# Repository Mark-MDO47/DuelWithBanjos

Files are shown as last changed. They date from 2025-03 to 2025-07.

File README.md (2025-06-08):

# DuelWithBanjos
Just for fun - tiny scarecrow skeletons playing banjo music, placed under the control of the UniRemote!
- https://github.com/Mark-MDO47/UniRemote
- DuelWithBanjos now at version V1.0!

A quick 38-second video demonstration:
- https://youtu.be/nwAhtAX-E6E

A story-line showing how to do Over-The-Air (OTA) Web updates to the Banjo Player ESP32.
- https://github.com/Mark-MDO47/DuelWithBanjos/blob/master/code/DuelWithBanjos/OTA_story.md

| My two little banjo players - BEFORE | My two little banjo players - AFTER<br>with new electronics and sound |
| --- | --- |
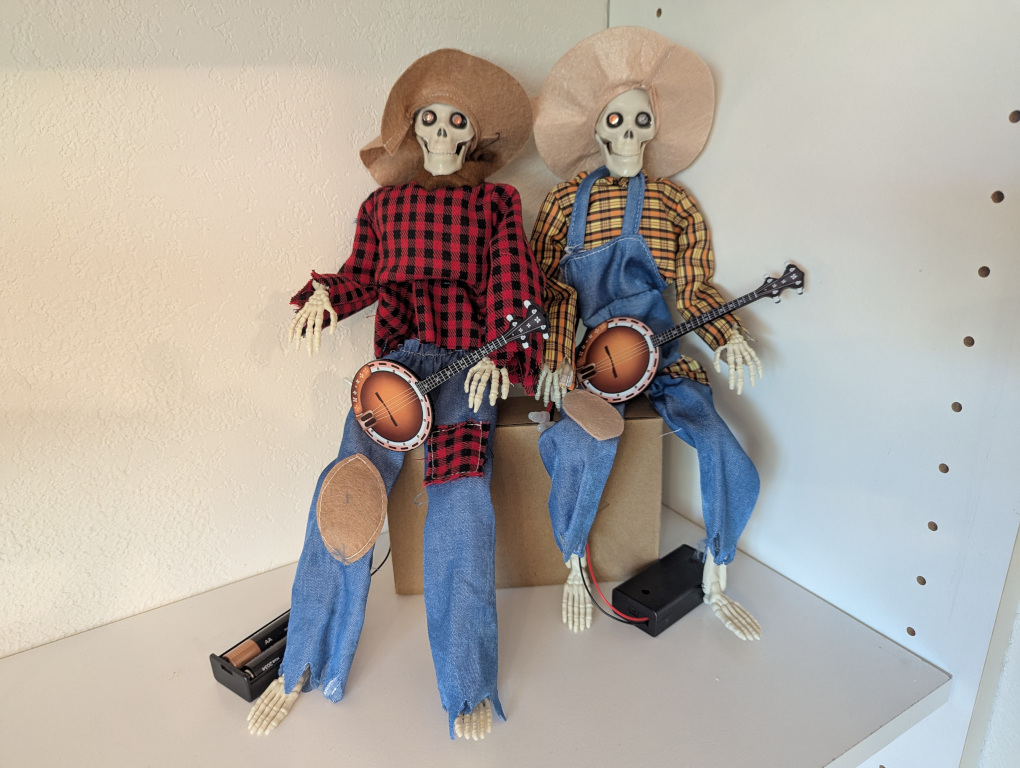
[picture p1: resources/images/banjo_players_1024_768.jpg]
My Banjo Players BEFORE
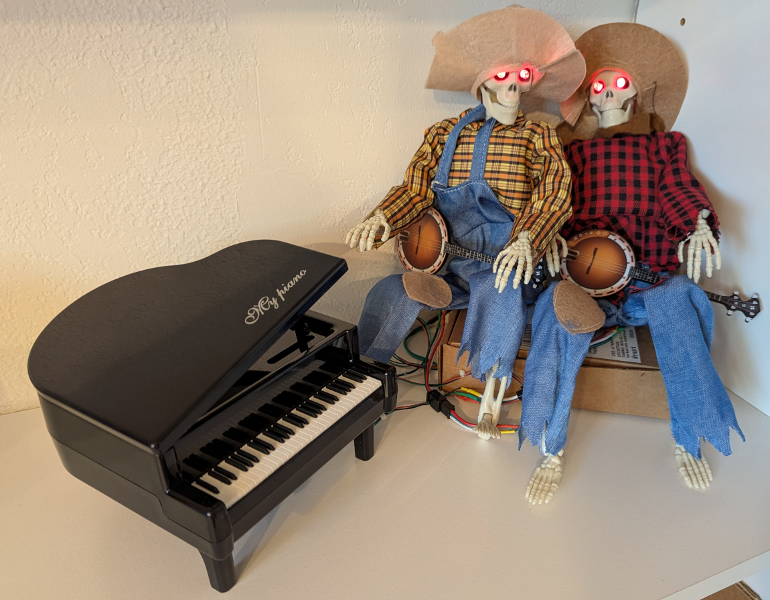
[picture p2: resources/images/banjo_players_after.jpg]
My Banjo Players AFTER upgrade
|  |  |
| **The new electronics on a prototype board** | **The new electronics inside the cardboard box** |
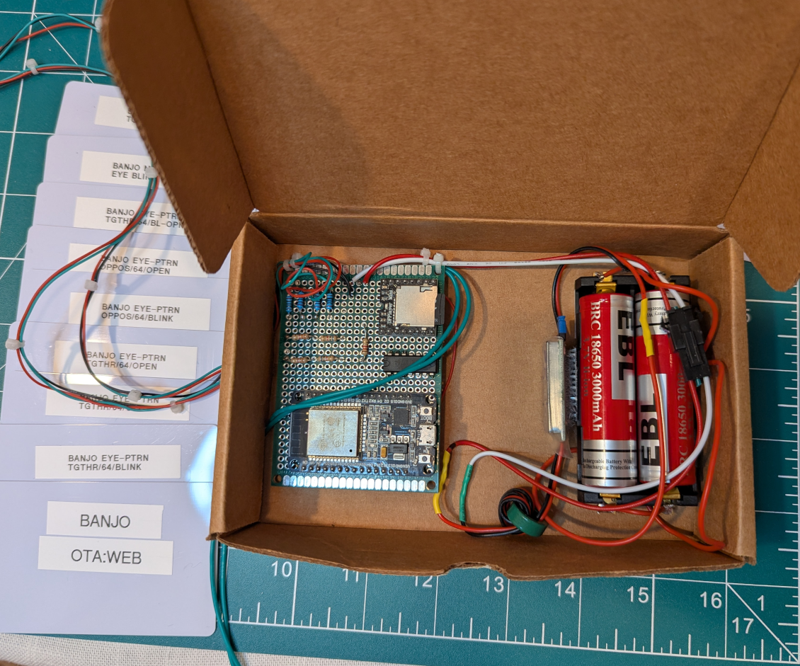
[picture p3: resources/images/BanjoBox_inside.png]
Banjo Player electronics inside cardboard box
| My ProtoBoard Banjo Player electronics |  |

**Table Of Contents**
* [Top](#duelwithbanjos "Top")
* [Introduction](#introduction "Introduction")
* [Schematic](#schematic "Schematic")
  * [Do-It-Yourself Layout Creator](#do\-it\-yourself-layout-creator "Do-It-Yourself Layout Creator")
* [Code](#code "Code")
* [Parts List](#parts-list "Parts List")
* [License](#license "License")

## Introduction
[Top](#duelwithbanjos "Top")<br>
I have two country style skeleton banjo players approximately 14 inches tall ordered from Amazon.com but apparently that exact model is no longer available there.
I think they might be similar to this one:
- https://www.amazon.com/XINANDHAO-Halloween-Animated-Skeletons-Musicians/dp/B0DC56RL1F

Version V1.0 includes the following capabilities:
- respond to controls from my UniRemote remote controller via ESP-NOW
  - https://github.com/Mark-MDO47/UniRemote
- play music using a YX5200 Audio Player which reads sound files from a MicroSD card
  - https://github.com/Mark-MDO47/AudioPlayer-YX5200
- blink LED "eyes" using Pulse Width Modulation (PWM)
  - https://github.com/Mark-MDO47/DuelWithBanjos/tree/master/code/LEDPinsPwmTemplate
- Have volume control for the sound
  - Fixed my bug; this now seems to work! I may make it more elaborate later.
- support Over-The-Air (OTA) re-programming
  - https://github.com/Mark-MDO47/DuelWithBanjos/blob/master/code/DuelWithBanjos/OTA_story.md
  - https://github.com/Mark-MDO47/UniRemote/blob/master/code/mdo_use_ota_webupdater/README.md

The future plan is to make them
- support OTA debugging via the extension "Visual Micro" for Visual Studio Code
  - I am still working on it - getting ESP-NOW, ota_webupdater, and OTA debugging to play together
  - https://www.visualmicro.com/
  - https://code.visualstudio.com/

## Schematic
[Top](#duelwithbanjos "Top")<br>
This is the schematic of the interesting part of the design, including the ESP32 module, sound control, and LED control.<br>
- The ESP32 of course has I/O at the 3.3V rail. The YX5200 uses 5V power and TTL voltage levels, which could be up to 5V.
  -  I use resistor networks to drop the YX5200 output voltages from 5V to 3.3V to be compatible with the ESP32 inputs. The ESP32 is **NOT** 5V tolerant on its inputs.
  -  The YX5200 is nominally able to work with TTL-level inputs (and 3.3V should be fine), but I use a SN74HCT125N quadruple bus buffer to raise voltages from 3.3V to 5V. I have had some issues with ESP32 outputs to WS2812B in the past and just like to beef the signal up to avoid problems.
- The 1K resistor in the path to the YX5200 RX line prevents coupling of digital noise into the sound output.
- I had to move to ESP32 pin D26 because of my horrible soldering.
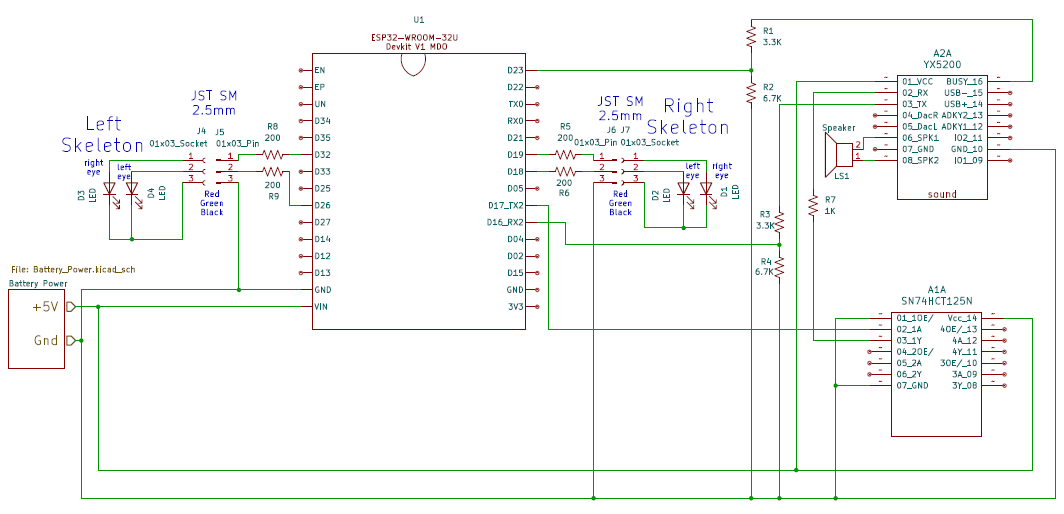
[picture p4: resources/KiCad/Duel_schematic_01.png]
Schematic of ESP32 module, sound control, and LED control


### Do-It-Yourself Layout Creator
[Top](#uniremote-\--one-remote-to-rule-them-all "Top")<br>
I didn't know about this when I did my perfboard design for Dueling with Banjos but I wish I had used DIYLC instead of hacking away at my perfboard!
- https://github.com/bancika/diy-layout-creator
- https://github.com/bancika/diy-layout-creator/releases

Here is a nice YouTube showing how to use it
- Design Circuits on Stripboard or Veroboard for FREE with DIY Layout Creator by TekSparkz - https://www.youtube.com/watch?v=mzje3eHqi2E

## Code
[Top](#duelwithbanjos "Top")<br>
The code is starting to take shape; you can find it here
- https://github.com/Mark-MDO47/DuelWithBanjos/tree/master/code/DuelWithBanjos

I wanted my PWM LED control to be automatic in between commands but also to respond to commands. I made some code to do this. Once everything is initialized, you only need to call **led_pins_pwm()** periodically from loop() to have the LED eyes follow the requested time pattern.
- https://github.com/Mark-MDO47/DuelWithBanjos/tree/master/code/LEDPinsPwmTemplate

## Parts List
[Top](#duelwithbanjos "Top")<br>
Work In Progress...

| Title | Descrip | URL | each |
| --- | --- | --- | --- |
| Skeletons | 2 @ Pose-able banjo playing skeletons | https://www.amazon.com/XINANDHAO-Halloween-Animated-Skeletons-Musicians/dp/B0DC56RL1F | $10.00 |
| ESP32 | 1 @ ESP32 Devkit V1 ESP-WROOM-32 | https://www.amazon.com/Hosyond-ESP-WROOM-32-Development-Microcontroller-Compatible/dp/B0C7C2HQ7P/ref=sr_1_4 | $3.50 |
| YX5200 | 1 @ Sound Module with MicroSD (TF) card socket | https://www.amazon.com/Organizer-YX5200-DFPlayer-Supporting-Arduino/dp/B07XXYQBNS/ref=sr_1_1 | $2.00 |
| SN74HCT125N | 1 @ Non-inverting 5.5V buffer 14-pin DIP | https://www.digikey.com/en/products/detail/texas-instruments/SN74HCT125N/376860 | $0.63 |
| Proto Board | 1 @ 3.125" x 2.25" Prototype Board | from deep in my closet | $ who-knows? |
| speaker |  Metal Shell Round Internal Magnet Speaker 2W 8 Ohm approx 1 inch | https://www.amazon.com/dp/B0177ABRQ6 | $2.80 |
| JST SM 2.5mm | 2 @ pair JST SM 2.5mm 3-pin Male/Female connectors and cables for banjo players | https://www.amazon.com/mxuteuk-Connectors-Connector-Adapter-Electrical/dp/B0DHKC3ZSF/ref=sr_1_2?th=1 | $0.45 |
| resistors | 4 @ 200-Ohm 1/4 watt through-hole resistors | https://www.digikey.com/en/products/filter/through-hole-resistors/53?s=N4IgTCBcDaIE4FMDOBLJAXA9nEBdAvkA | $0.10 |
| resistors | 1 @ 1.0-KOhm 1/4 watt through-hole resistors | https://www.digikey.com/en/products/detail/stackpole-electronics-inc/CF14JT1K00/1741314 | $0.10 |
| resistors | 2 @ 3.3-KOhm 1/4 watt through-hole resistors | https://www.digikey.com/en/products/detail/stackpole-electronics-inc/CF14JT3K30/1741376 | $0.10 |
| resistors | 2 @ 6.65-KOhm 1/4 watt through-hole resistors | https://www.digikey.com/en/products/detail/stackpole-electronics-inc/RNF14FTD6K65/1682364 | $0.10 |
| on/off latch button | 1 @ ON/Off Switch Self-Lock Micro Push Button Switch DC 30V 1A | https://www.amazon.com/gp/product/B086L2GPGX | $0.20 |
| UBEC 5V | 1 @ 5V/6V HOBBYWING 3A UBEC | https://www.aliexpress.us/item/3256805502614547.html | $1.50 |
| 18650 Battery | 2 @ 3.7V 18650 & charger<br>URL has 4 batteries plus charger so price each is inflated | https://www.amazon.com/dp/B0CP6V26QX | $5.00 |
| 18650 2-slot holder | 18650 Battery Holder 2 Slot 3.7V 18650 Battery | https://www.amazon.com/dp/B09LC13D9P | $2.60 |
| JST SM 2.5mm | 1 @ pair JST SM 2.5mm 3-pin Male/Female connectors and cables for power connection | https://www.amazon.com/mxuteuk-Connectors-Connector-Adapter-Electrical/dp/B0DHKC3ZSF/ref=sr_1_2?th=1 | $0.45 |

## License
[Top](#duelwithbanjos "Top")<br>
This repository has a LICENSE file for the Apache 2.0 License. There may be code included that I have modified from other open sources (such as Arduino, Espressif, SparkFun, Seeed Studio, DFRobot, RandomNerds, etc.). These other sources may possibly be licensed using a different license model. In such a case I will include some notation of this. Typically I will include verbatim the license in the included/modified source code, but alternatively there might be a LICENSE file in the source code area that points out exceptions to the Apache 2.0 License.

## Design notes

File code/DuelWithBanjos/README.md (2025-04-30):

# Duel With Banjos Code

My Banjo Players

**Table Of Contents**
* [Top](#duel-with-banjos-code "Top")
* [The Banjo Players](#the-banjo-players "The Banjo Players")
* [YX5200 Audio Player](#yx5200-audio-player "YX5200 Audio Player")
  * [The Music](#the-music "The Music")
  * [LICENSE for DFRobot code](#license-for-dfrobot-code "LICENSE for DFRobot code")
* [ESP32 LEDC PWM - LED Dimmer Control](#esp32-ledc-pwm-\--led-dimmer-control "ESP32 LEDC PWM - LED Dimmer Control")
* [UniRemote and ESP-NOW](#uniremote-and-esp\-now "UniRemote and ESP-NOW")
* [Over-The-Air Update](#over\-the\-air-update "Over-The-Air Update")
* [ESP32](#esp32 "ESP32")

## The Banjo Players
[Top](#duel-with-banjos-code "Top")<br>
I have two country style skeleton scarecrow banjo players approximately 14 inches tall ordered from Amazon.com but apparently that exact model is no longer available there.
I think they might be similar to this one:
- https://www.amazon.com/XINANDHAO-Halloween-Animated-Skeletons-Musicians/dp/B0DC56RL1F

The ones I have each have a 3V power supply and two very bright red LED eyes. There is no other electronics involved in them.

## YX5200 Audio Player
[Top](#duel-with-banjos-code "Top")<br>
I am providing sound for my banjo players using the YX5200 Audio Player, which is widely available from many sources. A MicroSD card is used to store the sound files.

There are some tricks to using this device in a way that many of the variants work. You may be interested to look in my repo here:
- https://github.com/Mark-MDO47/AudioPlayer-YX5200

Top view pin arrangement on YX5200 module

The music and sounds on the MicroSD card are either purchased by me or recorded/created by me. Attributions are present on the MicroSD card. The sound files are not included in this repository in respect of the copyright of the owners.

### The Music
[Top](#duel-with-banjos-code "Top")<br>
Currently the music includes
- Dueling Banjos by Curtis Mcpeake from **Curtis Mcpeake Plays Dueling Banjos & Other Bluegrass Favorites**
- Several selections from Todd Taylor's **Todd Taylor's Banjo Christmas**
- Several selections from **The Essential Patriotic Collection**
- Several selections from Garrick Ohlsson's **The Complete Chopin Piano Works Volume 10: Etudes**
- Several selections from Claudio Arrau's **Chopin: The Complete Nocturnes/The Complete Impromptus**
- A selection from Ingrid Filter's **Frederic Chopin Preludes**

### LICENSE for DFRobot code
[Top](#duel-with-banjos-code "Top")<br>
The DFRobot code (see https://www.dfrobot.com/) is not under the Apache License 2.0<br>
The license for the DFRobot code is copied into the file LICENSE_for_DFRobot_code.txt

## ESP32 LEDC PWM - LED Dimmer Control
[Top](#duel-with-banjos "Top")<br>
I am using the Espressif ESP32 Pulse Width Modulation (PWM) LED control to make the LED eyes do something interesting. This capability is similar to that available on Arduinos such as the Arduino Uno, but is specifically tailored to the ESP32. Be sure to use the new "pin-oriented" calling sequence instead of the earlier "channel-oriented" calling sequence.
- https://docs.espressif.com/projects/esp-idf/en/v5.4/esp32/api-reference/peripherals/ledc.html
- https://github.com/espressif/arduino-esp32/blob/master/docs/en/migration_guides/2.x_to_3.0.rst#ledc

You can see my method (still being refined) for having the LEDC PWM patterns play themselves here
- https://github.com/Mark-MDO47/DuelWithBanjos/blob/master/code/LEDPinsPwmTemplate/README.md

## UniRemote and ESP-NOW
[Top](#duel-with-banjos-code "Top")<br>
I am using UniRemote and its ESP-NOW WiFi capability as the remote control for this project
- https://github.com/Mark-MDO47/UniRemote

Image of UniRemote breadboard overview

This means I include the *.cpp and *.h from UniRemoteRcvrTemplate
- https://github.com/Mark-MDO47/UniRemote/tree/master/code/UniRemoteRcvrTemplate
- https://github.com/Mark-MDO47/UniRemote/blob/master/code/UniRemoteRcvrTemplate/README.md

## Over-The-Air Update
[Top](#duel-with-banjos-code "Top")<br>
This code supports Over-The-Air (OTA) Web Update. The OTA code comes from my UniRemote project.
- https://github.com/Mark-MDO47/UniRemote

Here is a story-line showing how to do OTA Web updates to the Banjo Player ESP32.
- https://github.com/Mark-MDO47/DuelWithBanjos/blob/master/code/DuelWithBanjos/OTA_story.md

## ESP32
[Top](#duel-with-banjos-code "Top")<br>
Both the LEDC library and the UniRemote ESP-NOW usage mean that the processor for this project will be an ESP32. I will use some variant of the original ESP32 Devkit V1 ESP-WROOM-32 because they are inexpensive and I have several of them hanging around my mad scientist laboratory just waiting to be put to use.

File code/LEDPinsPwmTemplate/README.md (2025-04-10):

# LEDPinsPwmTemplate - My Method to Use LEDC PWM

**Table Of Contents**
* [Top](#ledpinspwmtemplate-\--my-method-to-use-ledc-pwm "Top")
* [Intro](#intro "Intro")
* [Constants](#constants "Constants")
  * [Modifiable Constants](#modifiable-constants "Modifiable Constants")
  * [Do Not Change These Constants](#do-not-change-these-constants "Do Not Change These Constants")
* [Data Structures](#data-structures "Data Structures")
  * [Typedef for Pattern Step](#typedef-for-pattern-step "Typedef for Pattern Step")
  * [Typedef for Pins Controlled by LEDPinsPwmTemplate](#typedef-for-pins-controlled-by-ledpinspwmtemplate "Typedef for Pins Controlled by LEDPinsPwmTemplate")
* [Function Declarations](#function-declarations "Function Declarations")
  * [led_pins_pwm_init - in setup do hardware initialization](#led_pins_pwm_init-\--in-setup-do-hardware-initialization "led_pins_pwm_init - in setup do hardware initialization")
  * [led_pin_pwm_init_ptrn - in loop or setup start a pattern for a particular pin](#led_pin_pwm_init_ptrn-\--in-loop-or-setup-start-a-pattern-for-a-particular-pin "led_pin_pwm_init_ptrn - in loop or setup start a pattern for a particular pin")
  * [led_pins_pwm - in loop calculate PWM values and if changed output to hardware](#led_pins_pwm-\--in-loop-calculate-pwm-values-and-if-changed-output-to-hardware "led_pins_pwm - in loop calculate PWM values and if changed output to hardware")
  * [led_pin_pwm_set_pwm_scale - in loop or setup set global scale factor for PWM value](#led_pin_pwm_set_pwm_scale-\--in-loop-or-setup-set-global-scale-factor-for-pwm-value "led_pin_pwm_set_pwm_scale - in loop or setup set global scale factor for PWM value")
* [Debugging Functions](#debugging-functions "Debugging Functions")
  * [led_pin_pwm_set_dbg_enable - enable or disable debugging output](#led_pin_pwm_set_dbg_enable-\--enable-or-disable-debugging-output "led_pin_pwm_set_dbg_enable - enable or disable debugging output")
  * [led_pin_pwm_int_dbg_step - display debug info on state of pin and steps structures](#led_pin_pwm_int_dbg_step-\--display-debug-info-on-state-of-pin-and-steps-structures "led_pin_pwm_int_dbg_step - display debug info on state of pin and steps structures")

## Intro
[Top](#ledpinspwmtemplate-\--my-method-to-use-ledc-pwm "Top")<br>
This code is a vehicle for me to come up  with a general way to use LEDC PWM. I wanted to have a data structure for a time-sequence pattern that could be applied to a set of pins.

Many Arduinos, including the Arduino UNO and the ESP-32, can use LEDPinsPwm to control timing of LEDs. However, some Arduinos are more restrictive on things such as the PWM frequency allowed, so check your Arduino documentation.

LEDPinsPwmTemplate.ino is a near-minimum implementation of use of LEDPinsPwm. It has the following required parts:
- **#include "LEDPinsPwm.h"**
  - **optional**: you can edit LEDPinsPwm.h to change "modifiable" constants as outlined in that file. For instance, you can redefine LED_PINS_PWM_NUM_PINS to something other than 4.
- make the table **pwm_pin_info g_pwm_pin_info[LED_PINS_PWM_NUM_PINS]** to point to the pins you will be having LEDPinsPwm control. You must use this name and it must be global scope.
- provide storage for uint32_t **g_eyes_bright**. MS-16bits is numerator, LS-16bits is denominator for last call to led_pin_pwm_set_pwm_scale()
- make at least one **pwm_led_ptrn_step pattern**. This would be an array of pwm_led_ptrn_step, even if there is only one entry. These patterns can have any name you want; they will be referenced later
- in calls to led_pin_pwm_init_ptrn().
- in **setup()**, call **Serial.begin()** so that you can see error output and/or debug output in the serial monitor.
- in **setup()**, call **led_pins_pwm_init()** to connect to the hardware pins to control.
- in **loop()** (preferred) or **setup()**, call **led_pin_pwm_init_ptrn()** to set a pattern for each pin in **g_pwm_pin_info[]**. Only do this when initially setting or changing patterns for a pin.
- in **loop()**, call **led_pins_pwm()** to perform the patterns on the pins over time.
  - **optional**: later on you can call **led_pin_pwm_init_ptrn()** to set a new pattern for a pin or restart the existing pattern for a pin.
  - **optional**: later on you can call **led_pin_pwm_set_pwm_scale()** to set a global scale factor for the PWM values.

The following excerpts from LEDPinsPwmTemplate.ino illustrate the above steps.

```C
#include "LEDPinsPwm.h"

/////////////////////////////////////////////////////////////////////////////////////////////////////////
// pin definitions - name must be must be g_pwm_pin_info, must be one row for each PWM LED output pin
//
pwm_pin_info g_pwm_pin_info[LED_PINS_PWM_NUM_PINS] = {
  { .pin_num=18, .ptrn_step_ptr = (pwm_led_ptrn_step *)0, .idx_curr_step=0, .curr_pwm_val=0, .prev_pwm_val = 0xFFFF, .scale_factor=TIME_SCALE_EQUAL, .scaledtm_tick_incr = 0, .scaledtm_next_tick=0, .scaledtm_next_step=0 },
  { .pin_num=19, .ptrn_step_ptr = (pwm_led_ptrn_step *)0, .idx_curr_step=0, .curr_pwm_val=0, .prev_pwm_val = 0xFFFF, .scale_factor=TIME_SCALE_EQUAL, .scaledtm_tick_incr = 0, .scaledtm_next_tick=0, .scaledtm_next_step=0 },
  { .pin_num=32, .ptrn_step_ptr = (pwm_led_ptrn_step *)0, .idx_curr_step=0, .curr_pwm_val=0, .prev_pwm_val = 0xFFFF, .scale_factor=TIME_SCALE_EQUAL, .scaledtm_tick_incr = 0, .scaledtm_next_tick=0, .scaledtm_next_step=0 },
  { .pin_num=33, .ptrn_step_ptr = (pwm_led_ptrn_step *)0, .idx_curr_step=0, .curr_pwm_val=0, .prev_pwm_val = 0xFFFF, .scale_factor=TIME_SCALE_EQUAL, .scaledtm_tick_incr = 0, .scaledtm_next_tick=0, .scaledtm_next_step=0 }
};

/////////////////////////////////////////////////////////////////////////////////////////////////////////
// pwm LED pattern definitions - name can be anything, can be as many pattern definitions as desired,
//         can have as many steps per pattern as desired
//
pwm_led_ptrn_step pwm_ptrn_open_eye[] = { 
  { .start_set_pwm=0,                      .step_incr=1,  .step_time=1757, .tick_time=5, .tick_pwm= 2},
  { .start_set_pwm=LED_PINS_PWM_NO_CHANGE, .step_incr=-1, .step_time=1000, .tick_time=5, .tick_pwm=-7}
};

uint32_t g_eyes_bright; // MS-16bits is <num>, LS-16bits is <den> for last call to led_pin_pwm_set_pwm_scale()

/////////////////////////////////////////////////////////////////////////////////////////////////////////
// setup()
void setup() {
  Serial.begin(115200);         // this serial communication is for general debug; set the USB serial port to 115,200 baud
  while (!Serial) {
    ; // wait for serial port to connect. Needed for native USB port only
  }
  delay(3000);
  Serial.println(""); // print a blank line in case there is some junk from power-on
  Serial.println("starting LEDPinsPwmTemplate");

  if (led_pins_pwm_init(LED_PINS_PWM_FREQ, LED_PINS_PWM_VAL_NUM_BITS)) {
    while (1) ;
  } // end if error in initialization

} // end setup()

/////////////////////////////////////////////////////////////////////////////////////////////////////////
// loop()
void loop() {
  static uint32_t first_time = 1;
  static uint32_t time_msec_first_loop = 0;
  static uint16_t prev_ten_sec = 65535;
  static pwm_led_ptrn_step* prev_ptrn_ptr = (pwm_led_ptrn_step *) 0;

  uint32_t time_msec_this_loop = millis();
  uint16_t ten_secs = (time_msec_this_loop-time_msec_first_loop) / 10000;

  // this if statement should be entered once every 10 seconds and the first time loop() is executed
  if  ((0 != first_time) || (ten_secs != prev_ten_sec)) {
    if (0 != first_time) {
      time_msec_first_loop = millis();
      ten_secs = (time_msec_this_loop-time_msec_first_loop) / 10000; // probably same answer but not if setup() takes too long
    }
    
    // this section executes every 10 seconds

    // it is optional to adjust global scaling while operating LEDs but we demonstrate it here
    led_pin_pwm_set_pwm_scale(1,5); // this is a good max brightness in my breadboard setup; could have been done is setup()
    // commented out below is a way to adjust the brightness to fade away
    //    this would set pwm global scaling to 1/1, 1/2, 1/3, 1/4, ... 1/(n)
    // led_pin_pwm_set_pwm_scale(1,1+ten_secs);

    // it is optional to change LED pattern while operating LEDs but we demonstrate it here
    // pattern changes every 10 seconds
    if (pwm_ptrn_open_eye != prev_ptrn_ptr) prev_ptrn_ptr = pwm_ptrn_open_eye;
    else                                    prev_ptrn_ptr = pwm_ptrn_blink;
    for (int pin_idx = 0; pin_idx < NUMOF(g_pwm_pin_info); pin_idx += 1) {
      // commented out time scale manipulation would make pins operate on different time scales
      led_pin_pwm_init_ptrn(pin_idx, prev_ptrn_ptr, 0, TIME_SCALE_EQUAL /* + pin_idx*2 */, 0);
    } // end for each pin_idx
    
    first_time = 0; // first_time only once
    prev_ten_sec = ten_secs;
  } // end if once every 10 seconds

  led_pins_pwm(); // if needed, adjust brightness of LED
  delay(1);
} // end loop()
```

## Constants
[Top](#ledpinspwmtemplate-\--my-method-to-use-ledc-pwm "Top")<br>

### Modifiable Constants
[Top](#ledpinspwmtemplate-\--my-method-to-use-ledc-pwm "Top")<br>
```C
/////////////////////////////////////////////////////////////////////////////////////////////////////////
// modifiable constants for led_pins_pwm LEDC PWM library to control the LED Eyes of the Banjo Players
//
#define LED_PINS_PWM_NUM_PINS 4        // number of LED pins to control
#define LED_PINS_PWM_FREQ 500          // Arduino Uno is ~490 Hz. ESP32 example uses 5,000Hz
#define LED_PINS_PWM_VAL_NUM_BITS 8    // Use same resolution as Uno (8 bits, 0-255) but ESP32 can go up to 16 bits (some versions less)
#define TIME_SCALE_EQUAL 64           // pwm_pin_info factors for time_ entries: millisec = (time_<whatever> / TIME_SCALE_EQUAL)
                                      // this allows a relatively smooth scaling of time by setting
                                      // 2^32millisec / 64 is about 18 hours, so that will exceed any gig time for the banjo players
```

### Do Not Change These Constants
[Top](#ledpinspwmtemplate-\--my-method-to-use-ledc-pwm "Top")<br>
```C
/////////////////////////////////////////////////////////////////////////////////////////////////////////
// constants for led_pins_pwm LEDC PWM library to control the LED Eyes of the Banjo Players
//
#define LED_PINS_PWM_NO_CHANGE 0xFFFF  // no change to current pwm value when init pattern (.start_set_pwm or init function)
#define LED_PINS_PWM_USE_PTRN  0xFFFE  // use pwm value from pattern step when init pattern (init function only)
#define LED_PINS_PWM_MAX_VALUE ((1 << LED_PINS_PWM_VAL_NUM_BITS)-1) // max pwm value (255 if LED_PINS_PWM_VAL_NUM_BITS is 8)
```

## Data Structures

### Typedef for Pattern Step
[Top](#ledpinspwmtemplate-\--my-method-to-use-ledc-pwm "Top")<br>
```C
/////////////////////////////////////////////////////////////////////////////////////////////////////////
// structure typedefs for led_pins_pwm LEDC PWM library to control the LED Eyes of the Banjo Players
typedef struct {
  uint16_t  start_set_pwm; // if not LED_PINS_PWM_NO_CHANGE, set pwm value to this
  int16_t   step_incr;     // if # >= 0, increment step counter by #; if # < 0 go to step "-# - 1"
  uint16_t  step_time;     // how long (millisec B4 scaling) until this step is complete
  uint16_t  tick_time;     // how long (millisec B4 scaling) between each tick
  int16_t   tick_pwm;      // how far and what direction for pwm value each tick_time
} pwm_led_ptrn_step;
```

### Typedef for Pins Controlled by LEDPinsPwmTemplate
[Top](#ledpinspwmtemplate-\--my-method-to-use-ledc-pwm "Top")<br>
```C
typedef struct {
  uint16_t pin_num;             // pin number executing this pattern
  pwm_led_ptrn_step * ptrn_step_ptr; // pointer to array of pwm_led_ptrn_step (steps)
  uint16_t idx_curr_step;       // index into array of steps for current step
  uint16_t curr_pwm_val;        // current pwm intensity from 0 to LED_PINS_PWM_MAX_VALUE
  uint16_t prev_pwm_val;        // previous pwm intensity from 0 to LED_PINS_PWM_MAX_VALUE
  uint32_t scale_factor;        // to stretch time. scale_factor == TIME_SCALE_EQUAL means no stretch
  uint32_t scaledtm_tick_incr;  // time (tick_time * TIME_SCALE_EQUAL) to increment scaledtm_next_tick
  uint32_t scaledtm_next_tick;  // time (millisec * TIME_SCALE_EQUAL) to start next tick
  uint32_t scaledtm_next_step;  // time (millisec * TIME_SCALE_EQUAL) to go to next step
} pwm_pin_info;

/////////////////////////////////////////////////////////////////////////////////////////////////////////
// we need the user to prepare this struct for us
//
extern pwm_pin_info g_pwm_pin_info[LED_PINS_PWM_NUM_PINS];
```

## Function Declarations
[Top](#ledpinspwmtemplate-\--my-method-to-use-ledc-pwm "Top")<br>

### led_pins_pwm_init - in setup do hardware initialization
[Top](#ledpinspwmtemplate-\--my-method-to-use-ledc-pwm "Top")<br>
```C
/////////////////////////////////////////////////////////////////////////////////////////////////////////
// led_pins_pwm_init() - initialize pwm pins and set value to zero
//
// parameters (* means optional, has default as shown in declaration):
//   p_pwm_freq          - Frequency to use in Hertz. Usually between 500 and 5,000
//   p_pwm_val_num_bits  - Number of bits for value. Usually between 8 and 14
//                         If this is  8 then pwm_val would be between 0 and 255
//                         If this is 12 then pwm_val would be between 0 and 4095
// * p_num_pwm_scale     - numerator for final pwm scaling
// * p_den_pwm_scale     - denominator for final pwm scaling - should NOT be zero
// * p_serial_debugging  - zero for no serial debugging, 1 for serial debugging
//
int16_t led_pins_pwm_init(uint16_t p_pwm_freq, uint16_t p_pwm_val_num_bits, uint16_t p_num_pwm_scale = 1, uint16_t p_den_pwm_scale = 1, uint16_t p_serial_debugging = 0);
```

### led_pin_pwm_init_ptrn - in loop or setup start a pattern for a particular pin
[Top](#ledpinspwmtemplate-\--my-method-to-use-ledc-pwm "Top")<br>
```C
/////////////////////////////////////////////////////////////////////////////////////////////////////////
// led_pin_pwm_init_ptrn() - initialize a pwm_pin_info entry for a particular pattern
//    Called once each time a new pattern is set for a particular p_pin_idx in g_pwm_pin_info
//
// parameters (* means optional, has default as shown in declaration):
//    p_pin_idx        - must be a valid pin idx in g_pwm_pin_info
//    p_ptrn_ptr       - must point to an array of steps, with at least (1+p_idx_start_step) steps in the array
// *  p_idx_start_step - usually 0, occasionally 1, I don't know why it would be > 1
// *  p_scale_factor   - = TIME_SCALE_EQUAL means use the pattern millisec counts as-is
//                       > TIME_SCALE_EQUAL means go faster than pattern by factor (p_scale_factor/TIME_SCALE_EQUAL)
//                       < TIME_SCALE_EQUAL means go slower than pattern by factor (p_scale_factor/TIME_SCALE_EQUAL)
//                       = 0 (special case) means stay on step p_idx_start_step forever and never tick
// *  p_pwm_val_init   - = LED_PINS_PWM_NO_CHANGE means leave curr_pwm_val alone, do not change it from current value
//                       = LED_PINS_PWM_USE_PTRN  means store the pattern start_set_pwm into curr_pwm_val
//                       = other         means store the parameter p_pwm_val_init into curr_pwm_val
//
void led_pin_pwm_init_ptrn(int p_pin_idx, pwm_led_ptrn_step* p_ptrn_ptr, uint16_t p_idx_start_step = 0, uint32_t p_scale_factor=TIME_SCALE_EQUAL, uint16_t p_pwm_val_init=LED_PINS_PWM_USE_PTRN);
```

### led_pins_pwm - in loop calculate PWM values and if changed output to hardware
[Top](#ledpinspwmtemplate-\--my-method-to-use-ledc-pwm "Top")<br>
```C
/////////////////////////////////////////////////////////////////////////////////////////////////////////
// led_pins_pwm() - do calculations and output values for pwm for all pins based on g_pwm_pin_info
//
// should have called led_pins_pwm_init() and each g_pwm_pin_info[pin_idx] should have called led_pin_pwm_init_ptrn()
//
void led_pins_pwm();
```

### led_pin_pwm_set_pwm_scale - in loop or setup set global scale factor for PWM value 
[Top](#ledpinspwmtemplate-\--my-method-to-use-ledc-pwm "Top")<br>
```C
/////////////////////////////////////////////////////////////////////////////////////////////////////////
// led_pin_pwm_set_pwm_scale() - set valid global values for pwm scaling during operation
//
// parameters:
//   MS-16bits p_pwm_scale  - numerator for final pwm scaling
//   LS-16bits p_pwm_scale  - denominator for final pwm scaling - should NOT be zero
//
// If consistency checks are OK (no zero denominator), sets the global brightness and
//   saves p_pwm_scale into external g_eyes_bright so the caller can easily implement
//   commands such as "brighter" or "dimmer" since the current brightness is available.
//
extern uint32_t g_eyes_bright; // MS-16bits is <num>, LS-16bits is <den> for last call to led_pin_pwm_set_pwm_scale()
void led_pin_pwm_set_pwm_scale(uint32_t p_pwm_scale);
```

## Debugging Functions
[Top](#ledpinspwmtemplate-\--my-method-to-use-ledc-pwm "Top")<br>

### led_pin_pwm_set_dbg_enable - enable or disable debugging output
[Top](#ledpinspwmtemplate-\--my-method-to-use-ledc-pwm "Top")<br>
```C
/////////////////////////////////////////////////////////////////////////////////////////////////////////
// led_pin_pwm_set_dbg_enable() - routine for debugging
//
//   p_enable - nonzero to enable led_pin_pwm debug prints; zero to disable
//
void led_pin_pwm_set_dbg_enable(uint16_t p_enable);
```

### led_pin_pwm_int_dbg_step - display debug info on state of pin and steps structures
[Top](#ledpinspwmtemplate-\--my-method-to-use-ledc-pwm "Top")<br>
```C
/////////////////////////////////////////////////////////////////////////////////////////////////////////
// led_pin_pwm_int_dbg_step() - internal routine for debugging, display steps at important steps
//
void led_pin_pwm_int_dbg_step(int p_pin_idx); // to keep the compiler happy
```

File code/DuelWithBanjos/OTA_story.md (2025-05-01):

# OTA:WEB Story

**Table Of Contents**
* [Top](#otaweb-story "Top")
* [My Adaptation of the ESP32 Example OTAWebUpdater.ino](#my-adaptation-of-the-esp32-example-otawebupdaterino "My Adaptation of the ESP32 Example OTAWebUpdater.ino")
* [The Story](#the-story "The Story")
  * [The Setup](#the-setup "The Setup")
  * [Send OTA-WEB Command](#send-ota\-web-command "Send OTA-WEB Command")
  * [Enter Login Credentials](#enter-login-credentials "Enter Login Credentials")
  * [Click on Choose File](#click-on-choose-file "Click on Choose File")
  * [Time to Click on the UPDATE Button](#time-to-click-on-the-update-button "Time to Click on the UPDATE Button")
  * [The Upload Completes, Banjo Player ESP32 Reboots and Disconnects from WiFi Router](#the-upload-completes,-banjo-player-esp32-reboots-and-disconnects-from-wifi-router "The Upload Completes, Banjo Player ESP32 Reboots and Disconnects from WiFi Router")

## My Adaptation of the ESP32 Example OTAWebUpdater.ino
[Top](#otaweb-story "Top")<br>
The idea is that the OTA Web Updater is not started until we receive an ESP-NOW
command **OTA:WEB**, then the ESP32 connects to the WiFi router (using the built-in SSID and credentials) and starts the web page.
Prior to that, it does not connect to any WiFi SSID. It uses ESP-NOW (which is point-to-point) to receive its commands.

In this implementation, it will probably hang if it cannot connect to the specified WiFi SSID.

## The Story
[Top](#otaweb-story "Top")<br>

### The Setup
[Top](#otaweb-story "Top")<br>
My two little Banjo Players. We will re-program Over-The-Air the Banjo Player ESP32 (in the box).<br>
My Banjo Players

From the Arduino IDE, export the sketch you want to upload as **compiled binary**.<br>
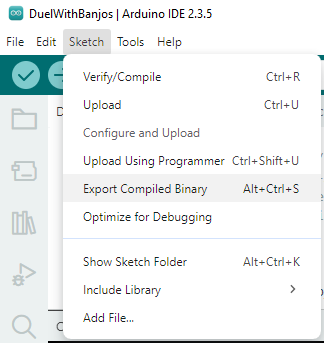
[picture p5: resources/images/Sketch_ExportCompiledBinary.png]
Export sketch as compiled binary


The UniRemoteCYD and the PICC card with the OTA:WEB command for the Banjo Players. The OTA:WEB command causes the Banjo Players to connect to the WiFi Router and start the login page website for Over-The-Air loading.<br>
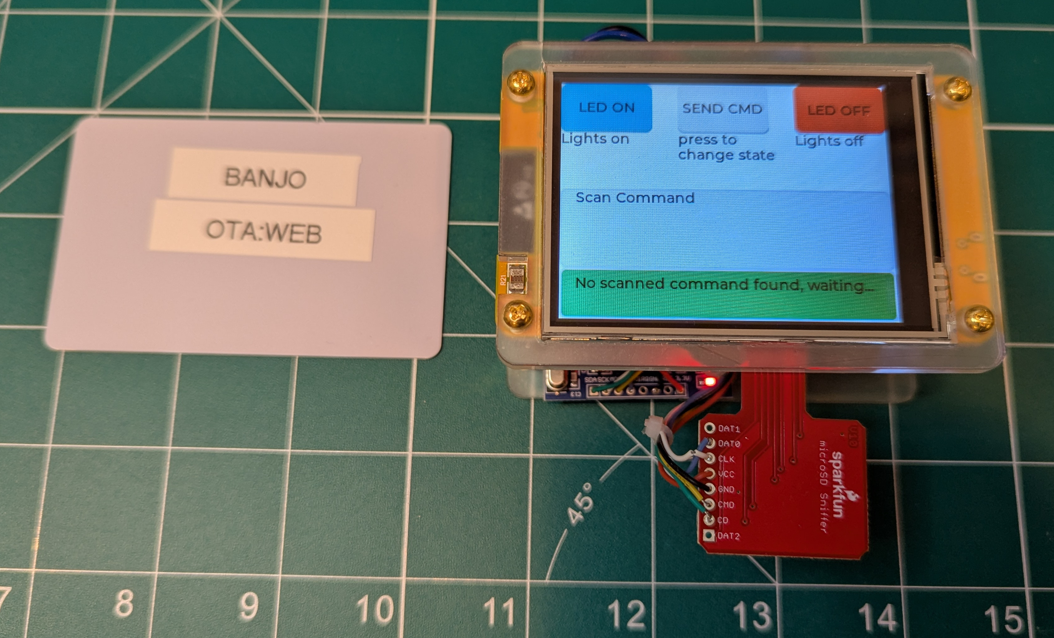
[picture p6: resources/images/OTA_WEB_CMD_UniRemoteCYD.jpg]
UniRemoteCYD and OTA:WEB command card


Before sending the OTA:WEB command, the Banjo Players have not connected to the WiFi router.  On your browser, you can either enter http://esp32.local/ or (if known) the IP address in the form w.x.y.z. At this time the browser cannot find the website for OTA loading because we have not yet commanded OTA:WEB.<br>
| Browser Webpage |
| --- |
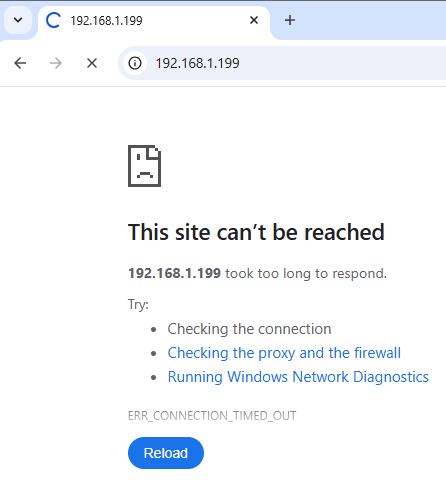
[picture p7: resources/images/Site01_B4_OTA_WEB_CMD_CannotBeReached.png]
Before sending the OTA:WEB command the website is not available.
|  |

### Send OTA-WEB Command
[Top](#otaweb-story "Top")<br>
After sending the OTA:WEB command, the Banjo Players connect to the WiFi router and start the OTA loading website login page. On your browser, you can either enter http://esp32.local/ or (if known) the IP address in the form w.x.y.z. Refreshing the browser will show the page.<br>
| Browser Webpage |
| --- |
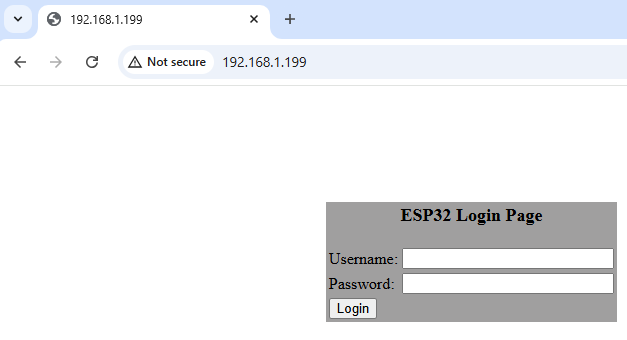
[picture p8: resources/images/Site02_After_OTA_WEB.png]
After sending the OTA:WEB command the website is available.
|  |

### Enter Login Credentials
[Top](#otaweb-story "Top")<br>
After entering login credentials, the OTA upload page appears.<br>
| Browser Webpage |
| --- |
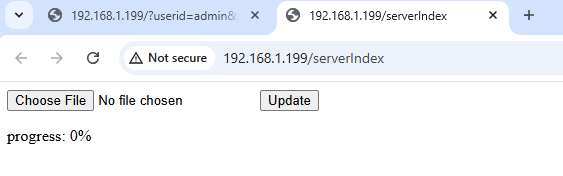
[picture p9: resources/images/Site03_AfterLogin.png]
After entering login credentials, the OTA upload page appears.
|  |

### Click on Choose File
[Top](#otaweb-story "Top")<br>
After clicking on the **Choose File** button and a standard open-file dialog box launches. Select the **"*.bin"** file you want to upload.<br>
| Browser Webpage |
| --- |
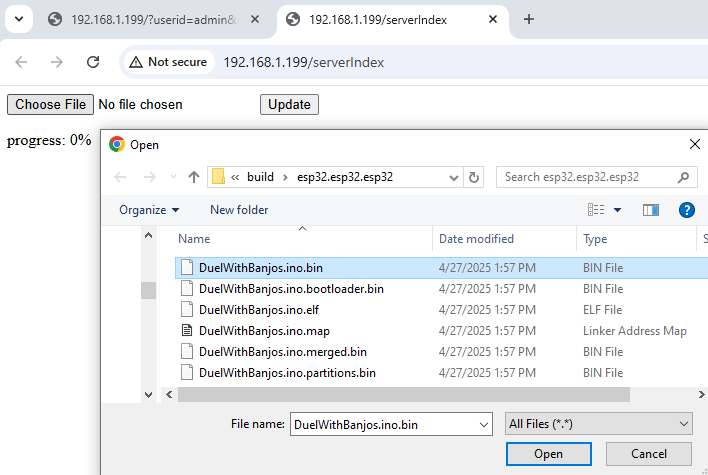
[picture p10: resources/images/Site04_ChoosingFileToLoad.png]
After clicking the choose-file button, a file brower opens.
|  |

### Time to Click on the UPDATE Button
The chosen file is displayed. Now click on the **UPDATE** button to start the upload.<br>
| Browser Webpage |
| --- |
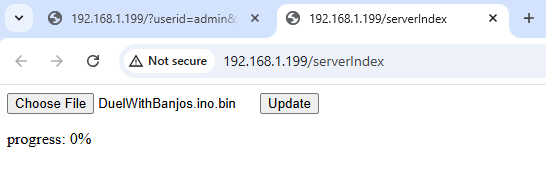
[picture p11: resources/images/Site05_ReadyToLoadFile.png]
Now ready to click on the UPDATE button.
|  |

The upload progress is displayed.<br>
| Browser Webpage |
| --- |
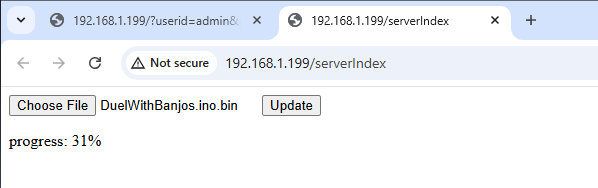
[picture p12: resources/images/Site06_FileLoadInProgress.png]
The upload progress is displayed.
|  |

### The Upload Completes, Banjo Player ESP32 Reboots and Disconnects from WiFi Router
[Top](#otaweb-story "Top")<br>
The Upload completes and the browser shows complete. The Banjo Player ESP32 reboots automatically. After reboot it does not connect to the WiFi Router until it receives another OTA:WEB command.<br>
| Browser Webpage |
| --- |
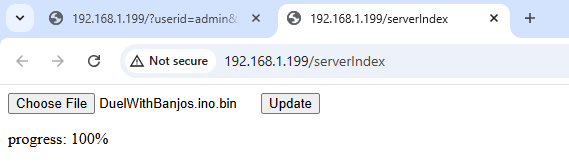
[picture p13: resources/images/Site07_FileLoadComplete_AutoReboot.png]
The Upload Completes, Banjo Player ESP32 Reboots and Disconnects from WiFi Router.
|  |

Refreshing the webpages will show that the Banjo Players are not serving the webpage anymore. In fact, they are not connected to the WiFi router at all.<br>
| Browser Webpage |
| --- |
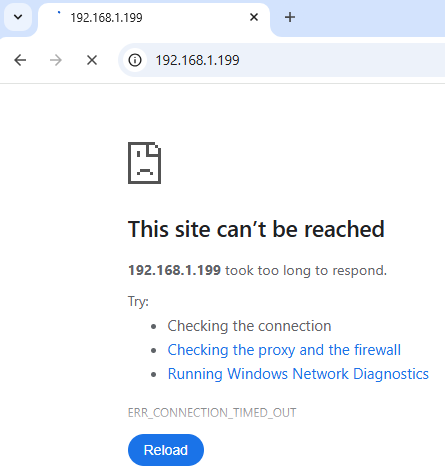
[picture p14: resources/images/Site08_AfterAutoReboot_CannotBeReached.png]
Banjo Player is not connected to the WiFi Router. Refresh of webpage shows not connected.
|  |

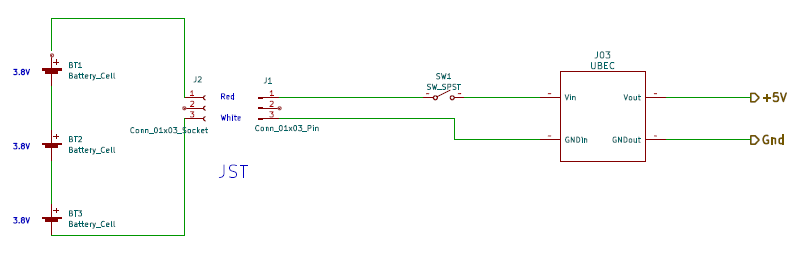
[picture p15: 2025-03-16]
resources/KiCad/Duel_schematic_02.png

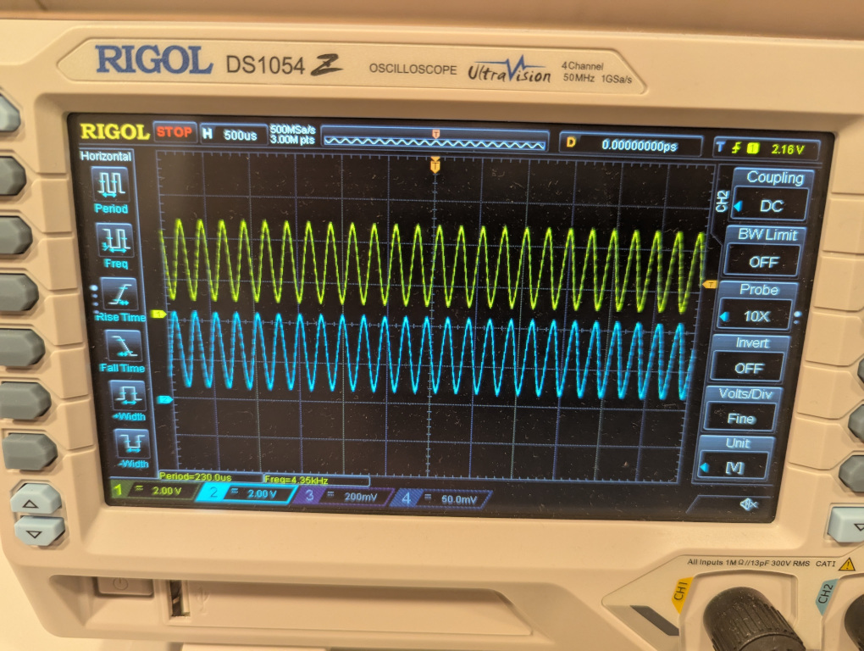
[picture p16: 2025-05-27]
resources/images/C4641_500usec_small.jpg

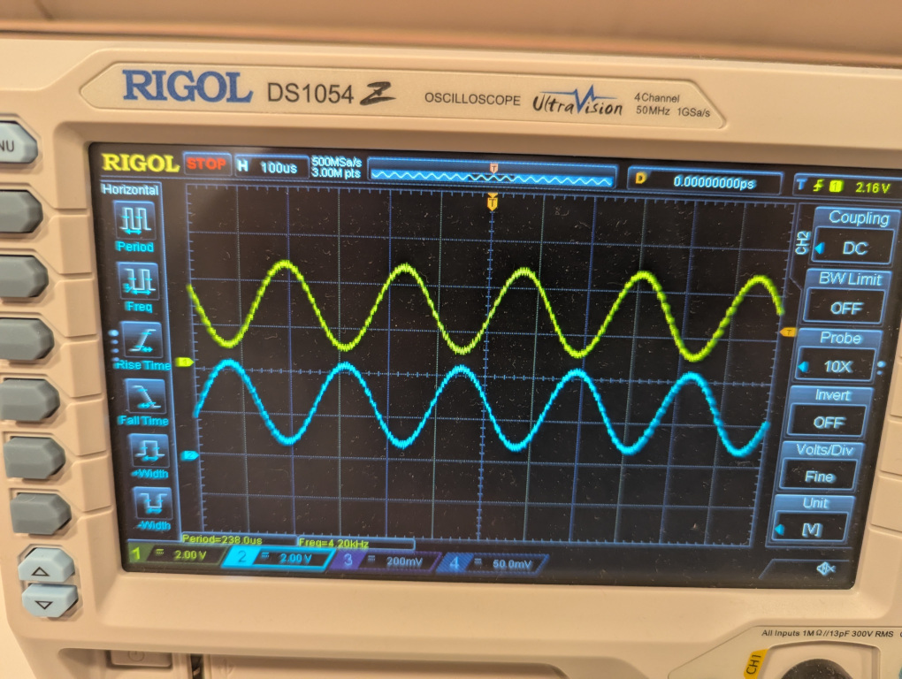
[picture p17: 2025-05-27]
resources/images/C4641_100usec_small.jpg

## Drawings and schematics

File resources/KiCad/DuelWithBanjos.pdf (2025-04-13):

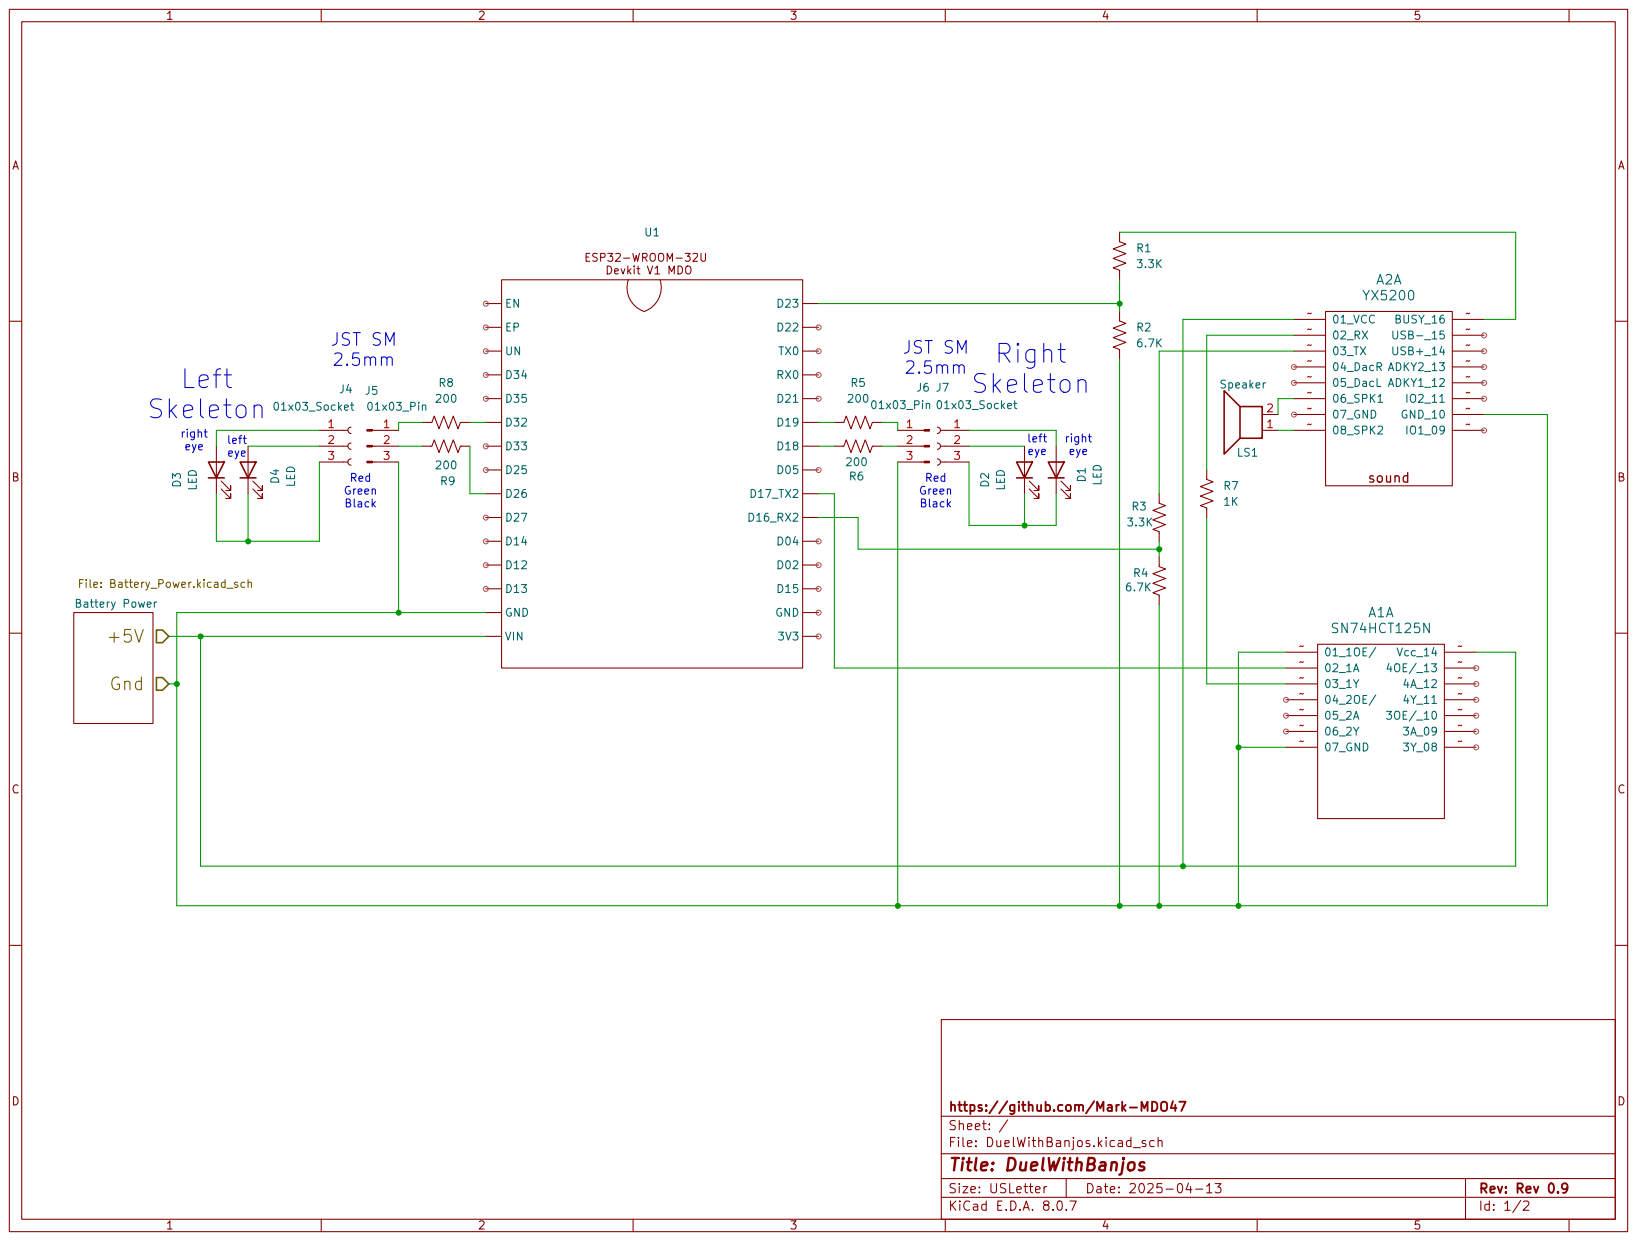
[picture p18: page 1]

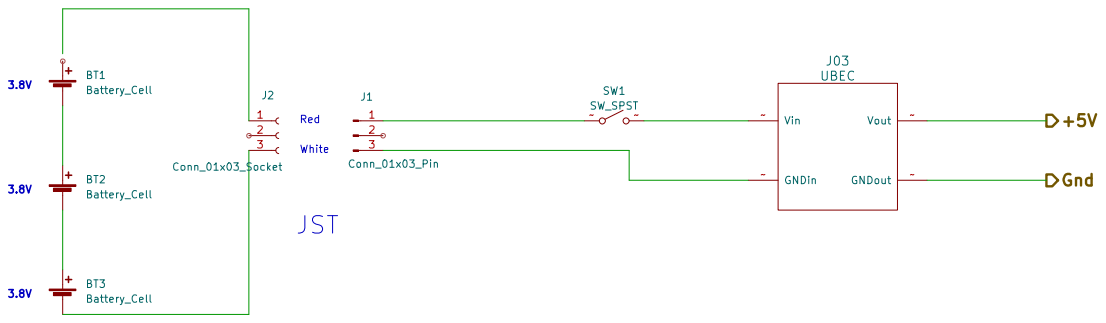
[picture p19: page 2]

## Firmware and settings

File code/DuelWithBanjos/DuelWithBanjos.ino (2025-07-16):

// DuelWithBanjos 2024
// Author: https://github.com/Mark-MDO47/
//

/*
   Copyright 2024, 2025 Mark Olson

   Licensed under the Apache License, Version 2.0 (the "License");
   you may not use this file except in compliance with the License.
   You may obtain a copy of the License at

       http://www.apache.org/licenses/LICENSE-2.0

   Unless required by applicable law or agreed to in writing, software
   distributed under the License is distributed on an "AS IS" BASIS,
   WITHOUT WARRANTIES OR CONDITIONS OF ANY KIND, either express or implied.
   See the License for the specific language governing permissions and
   limitations under the License.
 */

// The idea is to play a song such as "Dueling Banjos" repeatedly on the speaker.
//    Alternatively we can play banjo Christmas music or even turn the music off.
//    Actually any sort of music or sound would be possible.
// Additionally we will control and fade the banjo player LED eyes.

// We will use UniRemote to control our activities - see https://github.com/Mark-MDO47/UniRemote
//    Because UniRemote uses ESP-NOW, DuelWithBanjos must run on an ESP32.
//    We will use an inexpensive ESP-WROOM-32 and this guides us on selection of UART and GPIO pins
//       https://randomnerdtutorials.com/esp32-pinout-reference-gpios/
//       https://www.espressif.com/sites/default/files/documentation/esp32-wroom-32_datasheet_en.pdf

// This can be updated via an "OTA:WEB" ESP-NOW command, which will cause us to open a web page
//   on the specified SSID allowing Over-The-Air software update. That capability is based on
//   the ESP32 example OTAWebUpdater.ino

// connections:
//
// YX5200/DFPlayer Sound Player
//   ESP32 Dev Module pin D-16   DPIN_HWSRL_RX   Arduino RX; YX5200 TX - 9600 Baud
//   ESP32 Dev Module pin D-17   DPIN_HWSRL_TX   Arduino TX; YX5200 RX - 9600 Baud
//   ESP32 Dev Module pin D-23   DPIN_AUDIO_BUSY YX5200 BUSY; HIGH when audio finishes
//
// LED PWM
//   ESP32 Dev Module pin D-18   left  player left eye  (green)
//   ESP32 Dev Module pin D-19   left  player right eye (red)
//   ESP32 Dev Module pin D-32   right player left eye  (green)
//   ESP32 Dev Module pin D-26   right player right eye (red) (33 exceeded my soldering capability)

// Attributions for the sounds are on the MicroSD card containing the sounds.
// The music is either purchased or else performed/recorded by me.
// Purchased music at this time is as follows:
//    Dueling Banjos, Curtis McPeake 2009, https://www.amazon.com/Dueling-Banjos-CURTIS-OTHERS-MCPEAKE/dp/B0001MZ854
//    Todd Taylor's Banjo Christmas, Todd Taylor 2015, https://www.amazon.com/dp/1574243217

// See https://github.com/Mark-MDO47/AudioPlayer-YX5200 for details on using the YX5200/DFPlayer.
//   I usually install a copy of the DFRobot.com DFPlayer code when using it, since I did a lot
//   of debugging to find how to use it on all the variants of the YX5200 I have seen.
//   The still unmodified DFRobot.com DFPlayer code files are DFRobotDFPlayerMini.*.
//   LICENSE_for_DFRobot_code.txt shows it is OK to do this and describes the legal boundaries
//   for correct usage.

#include "Arduino.h"                // general Arduino definitions plus uint8_t etc.
#include <FastLED.h>                // only for the convenient EVERY_N_MILLISECONDS() macro - too lazy to write my own...

// mdo_use_ota_webupdater https://github.com/Mark-MDO47/UniRemote/tree/master/code/mdo_use_ota_webupdater
// This does not connect to WiFi router until it gets a command
#define MDO_USE_OTA 1               // zero to not use, non-zero to use OTA ESP32 Over-The-Air software updates

// Visual Micro Over-The-Air Debugging https://www.visualmicro.com/page/OTA-Debugging-for-Espressif-ESP-Boards.aspx
// For this we need to connect to WiFi all the time
//    NOTE: somehow this interferes with ESP-NOW and also does not make OTA debug work. It does put the IP address on the router.
#define VM_OTA_DEBUG 0              // zero to not use, non-zero to use OTA ESP32 debugging with Visual Micro and Microsoft Visual Studio

#if (MDO_USE_OTA || VM_OTA_DEBUG)
#include "mdo_use_ota_webupdater.h" // for mdo_use_ota_webupdater "library"
#endif // (MDO_USE_OTA || VM_OTA_DEBUG)
#include <UniRemoteRcvr.h>          // for UniRemoteRcvr "library"



#include "HardwareSerial.h"         // to talk with the YX5200
#include "DFRobotDFPlayerMini.h"    // to communicate with the YX5200 audio player
#include "SoundNum.h"               // numbers for each sound

#include "LEDPinsPwm.h"             // to control LED eyes with Pulse Width Modulation


////////////////////////////////////////////////////////////////////////////////////////
// definitions for YX5200/DFPlayer and ESP-WROOM-32 serial port and volume controls

#define DPIN_HWSRL_RX   16  // HW-serial in  - talk to DFPlayer audio player (YX5200)
#define DPIN_HWSRL_TX   17  // HW-serial out - talk to DFPlayer audio player (YX5200)
#define DPIN_AUDIO_BUSY 23  // digital input - HIGH when audio finishes
DFRobotDFPlayerMini myDFPlayer;                                // to talk to YX5200 audio player
void DFsetup();                                                // how to initialize myDFPlayer
constexpr uint32_t SOUND_ACTIVE_PROTECT = 200; // milliseconds to keep SW twiddled sound active after doing myDFPlayer.play(mySound)
uint32_t gTimerForceSoundActv = 0;             // SOUND_ACTIVE_PROTECT until millis() >= this

// Problem with dynamically setting volume - seems to prevent starting a different song until the current one finishes
#define VOLUME_ALLOW_CHANGE 0    // 1 if can dynamically set volume

#define VOLUME_GSCALE_DIVISOR 100
uint32_t g_volume_gscale = VOLUME_GSCALE_DIVISOR; // volume global scale factor. range: 0 to 200

constexpr uint16_t SOUND_VOL_MIN     =  0;  // range 0 to 30
constexpr uint16_t SOUND_VOL_MAX     = 30;  // range 0 to 30
constexpr uint16_t SOUND_VOL_DEFAULT = 25;  // default volume - range 0 to 30
uint16_t g_current_volume_set = SOUND_VOL_DEFAULT; // 

// #define DFPRINTDETAIL 1 // if need detailed status from myDFPlayer (YX5200 communications)
#define DFPRINTDETAIL 0  // will not print detailed status from myDFPlayer

#if DFPRINTDETAIL // routine to do detailed debugging
  void DFprintDetail(uint8_t type, int value); // definition of call
#else  // no DFPRINTDETAIL
  #define DFprintDetail(type, value) // nothing at all
#endif // #if DFPRINTDETAIL

uint16_t g_global_volume_scaling = 100;  // integer percentage volume (range 0 through 200)
uint16_t g_unscaled_volume;              // volume active now before scaling (range 0 thru 30)

typedef struct {
  char*    song_name;   // points to name of song to play
  uint16_t soundnum;    // number of sound
  uint16_t song_volume; // song-suggested volume
} music_song_to_soundnum_t;
static music_song_to_soundnum_t g_music_song_to_soundnum[] = {
  { .song_name = (char*)"DUEL-BANJO",                    .soundnum = SOUNDNUM_DuelingBanjos,                             .song_volume = SOUND_VOL_DEFAULT },
  { .song_name = (char*)"SILENCE",                       .soundnum = SOUNDNUM_silence,                                   .song_volume = SOUND_VOL_DEFAULT },
  { .song_name = (char*)"DECK-HALLS",                    .soundnum = SOUNDNUM_DeckTheDuelingHalls,                       .song_volume = SOUND_VOL_DEFAULT },
  { .song_name = (char*)"WHAT-CHILD",                    .soundnum = SOUNDNUM_WhatChildIsThis,                           .song_volume = SOUND_VOL_DEFAULT },
  { .song_name = (char*)"MERRY-GENTLEMEN",               .soundnum = SOUNDNUM_GodRestYe,                                 .song_volume = SOUND_VOL_DEFAULT },
  { .song_name = (char*)"TOWN-BETHLEHEM",                .soundnum = SOUNDNUM_OLittleTownOf,                             .song_volume = SOUND_VOL_DEFAULT },
  { .song_name = (char*)"KING-WENCESLAS",                .soundnum = SOUNDNUM_GoodKingWenceslas,                         .song_volume = SOUND_VOL_DEFAULT },
  { .song_name = (char*)"CHOPIN-ETUDE-TRISTESSE",        .soundnum = SOUNDNUM_Chopin_Etude_10_03,                        .song_volume = SOUND_VOL_DEFAULT },
  { .song_name = (char*)"CHOPIN-NOCTURNE-E-FLAT",        .soundnum = SOUNDNUM_Chopin_Noct_55_2,                          .song_volume = SOUND_VOL_DEFAULT },
  { .song_name = (char*)"CHOPIN-ETUDE-REVOLUTIONARY",    .soundnum = SOUNDNUM_Chopin_Etude_10_12,                        .song_volume = SOUND_VOL_DEFAULT },
  { .song_name = (char*)"CHOPIN-NOCTURNE-D-FLAT",        .soundnum = SOUNDNUM_Chopin_Noct_27_2,                          .song_volume = SOUND_VOL_DEFAULT },
  { .song_name = (char*)"CHOPIN-NOCTURNE-G",             .soundnum = SOUNDNUM_Chopin_Noct_37_2,                          .song_volume = SOUND_VOL_DEFAULT },
  { .song_name = (char*)"CHOPIN-PRELUDE-RAINDROP",       .soundnum = SOUNDNUM_Chopin_Prelude_15,                         .song_volume = SOUND_VOL_DEFAULT },
  { .song_name = (char*)"PATRIOT-BATTLE-HYMN-REPUBLIC",  .soundnum = SOUNDNUM_Patriotic_Battle_Hymn_of_the_Republic,     .song_volume = SOUND_VOL_DEFAULT },
  { .song_name = (char*)"PATRIOT-AMERICA-THE-BEAUTIFUL", .soundnum = SOUNDNUM_Patriotic_America_the_Beautiful,           .song_volume = SOUND_VOL_DEFAULT },
  { .song_name = (char*)"PATRIOT-JOHNNY-MARCHING-HOME",  .soundnum = SOUNDNUM_Patriotic_When_Johnny_Comes_Marching_Home, .song_volume = SOUND_VOL_DEFAULT },
  { .song_name = (char*)"PATRIOT-MARINE-HYMN",           .soundnum = SOUNDNUM_Patriotic_Marine_Hymn,                     .song_volume = SOUND_VOL_DEFAULT },
  { .song_name = (char*)"PATRIOT-DIXIE",                 .soundnum = SOUNDNUM_Patriotic_Dixie,                           .song_volume = SOUND_VOL_DEFAULT },
  { .song_name = (char*)"PATRIOT-SHENANDOAH",            .soundnum = SOUNDNUM_Patriotic_Shenandoah,                      .song_volume = SOUND_VOL_DEFAULT },
  { .song_name = (char*)"PATRIOT-STAR-SPANGLED-BANNER",  .soundnum = SOUNDNUM_Patriotic_Star_Spangled_Banner,            .song_volume = SOUND_VOL_DEFAULT },
  { .song_name = (char*)"A440",                          .soundnum = SOUNDNUM_A440_SIN_WAVE,                             .song_volume = SOUND_VOL_DEFAULT },
  { .song_name = (char*)"C4641",                         .soundnum = SOUNDNUM_C4641_SIN_WAVE,                            .song_volume = SOUND_VOL_DEFAULT },
  { .song_name = (char*)"SOUNDNUM_ERR_INVALID",          .soundnum = SOUNDNUM_ERR_INVALID,                               .song_volume = SOUND_VOL_DEFAULT }
};
typedef struct {
  char*     type_name;
  uint16_t* list_array;
  uint16_t  num_in_list;
} music_type_to_music_list_t;

uint16_t g_music_type_array_duel[] = { SOUNDNUM_DuelingBanjos };
uint16_t g_music_type_array_christmas[] = {
  SOUNDNUM_DeckTheDuelingHalls,
  SOUNDNUM_WhatChildIsThis,
  SOUNDNUM_GodRestYe,
  SOUNDNUM_OLittleTownOf,
  SOUNDNUM_GoodKingWenceslas
};
uint16_t g_music_type_array_chopin[] = {
  SOUNDNUM_Chopin_Etude_10_03,
  SOUNDNUM_Chopin_Noct_55_2,
  SOUNDNUM_Chopin_Etude_10_12,
  SOUNDNUM_Chopin_Noct_27_2,
  SOUNDNUM_Chopin_Noct_37_2,
  SOUNDNUM_Chopin_Prelude_15
};
uint16_t g_music_type_array_patriot[] = {
  SOUNDNUM_Patriotic_Battle_Hymn_of_the_Republic,
  SOUNDNUM_Patriotic_America_the_Beautiful,
  SOUNDNUM_Patriotic_When_Johnny_Comes_Marching_Home,
  SOUNDNUM_Patriotic_Marine_Hymn,
  SOUNDNUM_Patriotic_Dixie,
  SOUNDNUM_Patriotic_Shenandoah,
  SOUNDNUM_Patriotic_Star_Spangled_Banner
};
uint16_t g_music_type_array_all[] = {
  SOUNDNUM_DuelingBanjos,
  SOUNDNUM_DeckTheDuelingHalls,
  SOUNDNUM_WhatChildIsThis,
  SOUNDNUM_GodRestYe,
  SOUNDNUM_OLittleTownOf,
  SOUNDNUM_GoodKingWenceslas,
  SOUNDNUM_Chopin_Etude_10_03,
  SOUNDNUM_Chopin_Noct_55_2,
  SOUNDNUM_Chopin_Etude_10_12,
  SOUNDNUM_Chopin_Noct_27_2,
  SOUNDNUM_Chopin_Noct_37_2,
  SOUNDNUM_Chopin_Prelude_15,
  SOUNDNUM_Patriotic_Battle_Hymn_of_the_Republic,
  SOUNDNUM_Patriotic_America_the_Beautiful,
  SOUNDNUM_Patriotic_When_Johnny_Comes_Marching_Home,
  SOUNDNUM_Patriotic_Marine_Hymn,
  SOUNDNUM_Patriotic_Dixie,
  SOUNDNUM_Patriotic_Shenandoah,
  SOUNDNUM_Patriotic_Star_Spangled_Banner
};

uint16_t g_music_type_array_all_plus_invalid[] = {
  SOUNDNUM_DuelingBanjos,
  SOUNDNUM_DeckTheDuelingHalls,
  SOUNDNUM_WhatChildIsThis,
  SOUNDNUM_GodRestYe,
  SOUNDNUM_OLittleTownOf,
  SOUNDNUM_GoodKingWenceslas,
  SOUNDNUM_Chopin_Etude_10_03,
  SOUNDNUM_Chopin_Noct_55_2,
  SOUNDNUM_Chopin_Etude_10_12,
  SOUNDNUM_Chopin_Noct_27_2,
  SOUNDNUM_Chopin_Noct_37_2,
  SOUNDNUM_Chopin_Prelude_15,
  SOUNDNUM_Patriotic_Battle_Hymn_of_the_Republic,
  SOUNDNUM_Patriotic_America_the_Beautiful,
  SOUNDNUM_Patriotic_When_Johnny_Comes_Marching_Home,
  SOUNDNUM_Patriotic_Marine_Hymn,
  SOUNDNUM_Patriotic_Dixie,
  SOUNDNUM_Patriotic_Shenandoah,
  SOUNDNUM_Patriotic_Star_Spangled_Banner,
  SOUNDNUM_A440_SIN_WAVE,
  SOUNDNUM_C4641_SIN_WAVE,
  SOUNDNUM_ERR_INVALID
};

music_type_to_music_list_t g_music_type_to_music_list_duel      = { .type_name=(char*)"DUEL",      .list_array=&g_music_type_array_duel[0],      .num_in_list = NUMOF(g_music_type_array_duel) };
music_type_to_music_list_t g_music_type_to_music_list_christmas = { .type_name=(char*)"CHRISTMAS", .list_array=&g_music_type_array_christmas[0], .num_in_list = NUMOF(g_music_type_array_christmas) };
music_type_to_music_list_t g_music_type_to_music_list_chopin    = { .type_name=(char*)"CHOPIN",    .list_array=&g_music_type_array_chopin[0],    .num_in_list = NUMOF(g_music_type_array_chopin) };
music_type_to_music_list_t g_music_type_to_music_list_patriot   = { .type_name=(char*)"PATRIOT",   .list_array=&g_music_type_array_patriot[0],   .num_in_list = NUMOF(g_music_type_array_patriot) };
music_type_to_music_list_t g_music_type_to_music_list_all       = { .type_name=(char*)"ALL",       .list_array=&g_music_type_array_all[0],       .num_in_list = NUMOF(g_music_type_array_all) };

music_type_to_music_list_t* g_music_type_to_music_list_array[] = {
  &g_music_type_to_music_list_duel,
  &g_music_type_to_music_list_christmas,
  &g_music_type_to_music_list_chopin,
  &g_music_type_to_music_list_patriot,
  &g_music_type_to_music_list_all
};

constexpr uint16_t MUSIC_MODE_SINGLE_SONG  = 0;
constexpr uint16_t MUSIC_MODE_TYPE_OF_SONG = 1;
// constexpr uint16_t MUSIC_MODE_OFF       = 2; //  this is implemented by using SOUNDNUM_silence
uint16_t g_music_song_to_soundnum_idx_playing_now;              // kept current in all modes
uint16_t g_music_mode = MUSIC_MODE_SINGLE_SONG;
uint16_t g_music_soundnum_single_song = SOUNDNUM_DuelingBanjos; // only used if MUSIC_MODE_SINGLE_SONG
music_type_to_music_list_t* g_music_type_list;                  // only used if MUSIC_MODE_TYPE_OF_SONG
uint16_t g_music_type_list_idx_playing_now;                     // only used if MUSIC_MODE_TYPE_OF_SONG

/////////////////////////////////////////////////////////////////////////////////////////////////////////
// structures for LEDPinsPwm to control the LED Eyes of the Banjo Players

// pin definitions - name must be must be g_pwm_pin_info, must be one row for each PWM LED output pin
//
// [0] = left  skeleton, left eye
// [1] = left  skeleton, right eye
// [2] = right skeleton, left eye
// [3] = right skeleton, right eye
//
pwm_pin_info g_pwm_pin_info[LED_PINS_PWM_NUM_PINS] = {
  { .pin_num=18, .ptrn_step_ptr = (pwm_led_ptrn_step *)0, .idx_curr_step=0, .curr_pwm_val=0, .prev_pwm_val = 0xFFFF, .scale_factor=TIME_SCALE_EQUAL, .scaledtm_tick_incr = 0, .scaledtm_next_tick=0, .scaledtm_next_step=0 },
  { .pin_num=19, .ptrn_step_ptr = (pwm_led_ptrn_step *)0, .idx_curr_step=0, .curr_pwm_val=0, .prev_pwm_val = 0xFFFF, .scale_factor=TIME_SCALE_EQUAL, .scaledtm_tick_incr = 0, .scaledtm_next_tick=0, .scaledtm_next_step=0 },
  { .pin_num=32, .ptrn_step_ptr = (pwm_led_ptrn_step *)0, .idx_curr_step=0, .curr_pwm_val=0, .prev_pwm_val = 0xFFFF, .scale_factor=TIME_SCALE_EQUAL, .scaledtm_tick_incr = 0, .scaledtm_next_tick=0, .scaledtm_next_step=0 },
  { .pin_num=26, .ptrn_step_ptr = (pwm_led_ptrn_step *)0, .idx_curr_step=0, .curr_pwm_val=0, .prev_pwm_val = 0xFFFF, .scale_factor=TIME_SCALE_EQUAL, .scaledtm_tick_incr = 0, .scaledtm_next_tick=0, .scaledtm_next_step=0 }
};

// pwm LED pattern definitions - name can be anything, can be as many pattern definitions as desired,
//         can have as many steps per pattern as desired
//
pwm_led_ptrn_step g_pwm_ptrn_open_eye[] = { 
  { .start_set_pwm=0,                      .step_incr=1,  .step_time=1400, .tick_time=5, .tick_pwm= 0},
  { .start_set_pwm=0,                      .step_incr=1,  .step_time=1757, .tick_time=5, .tick_pwm= 2},
  { .start_set_pwm=LED_PINS_PWM_NO_CHANGE, .step_incr=-2, .step_time=1000, .tick_time=5, .tick_pwm=-7}
};
pwm_led_ptrn_step g_pwm_ptrn_blink[] = { 
  { .start_set_pwm=LED_PINS_PWM_MAX_VALUE, .step_incr=1,  .step_time=450, .tick_time=5, .tick_pwm= 0},
  { .start_set_pwm=0,                      .step_incr=1,  .step_time=450, .tick_time=5, .tick_pwm= 0},
  { .start_set_pwm=LED_PINS_PWM_MAX_VALUE, .step_incr=-2, .step_time=450, .tick_time=5, .tick_pwm= 0}
};

pwm_led_ptrn_step g_pwm_ptrn_sinelon0[] = { 
  { .start_set_pwm=0,                      .step_incr=2,  .step_time=500, .tick_time=5, .tick_pwm= 3},
  { .start_set_pwm=0,                      .step_incr=1,  .step_time=500, .tick_time=5, .tick_pwm= 3},
  { .start_set_pwm=LED_PINS_PWM_NO_CHANGE, .step_incr=-2, .step_time=500, .tick_time=5, .tick_pwm=-3}
};
pwm_led_ptrn_step g_pwm_ptrn_sinelon1[] = { 
  { .start_set_pwm=0,                      .step_incr=2,  .step_time=250, .tick_time=5, .tick_pwm= 0},
  { .start_set_pwm=0,                      .step_incr=1,  .step_time=500, .tick_time=5, .tick_pwm= 3},
  { .start_set_pwm=LED_PINS_PWM_NO_CHANGE, .step_incr=-2, .step_time=500, .tick_time=5, .tick_pwm=-3}
};
pwm_led_ptrn_step g_pwm_ptrn_sinelon2[] = {
  { .start_set_pwm=0,                      .step_incr=2,  .step_time=500, .tick_time=5, .tick_pwm= 0},
  { .start_set_pwm=0,                      .step_incr=1,  .step_time=500, .tick_time=5, .tick_pwm= 3},
  { .start_set_pwm=LED_PINS_PWM_NO_CHANGE, .step_incr=-2, .step_time=500, .tick_time=5, .tick_pwm=-3}
};
pwm_led_ptrn_step g_pwm_ptrn_sinelon3[] = {
  { .start_set_pwm=0,                      .step_incr=2,  .step_time=750, .tick_time=5, .tick_pwm= 0},
  { .start_set_pwm=0,                      .step_incr=1,  .step_time=500, .tick_time=5, .tick_pwm= 3},
  { .start_set_pwm=LED_PINS_PWM_NO_CHANGE, .step_incr=-2, .step_time=500, .tick_time=5, .tick_pwm=-3}
};
pwm_led_ptrn_step* g_pwm_ptrn_sinelon_ptrs[LED_PINS_PWM_NUM_PINS] = {g_pwm_ptrn_sinelon0, g_pwm_ptrn_sinelon1, g_pwm_ptrn_sinelon2, g_pwm_ptrn_sinelon3};

pwm_led_ptrn_step g_pwm_ptrn_off[] = {
  { .start_set_pwm=0,                      .step_incr=-1, .step_time=750, .tick_time=5, .tick_pwm= 0}
};

uint32_t g_eyes_bright; // MS-16bits is <num>, LS-16bits is <den> for led_pin_pwm_set_pwm_scale()
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
void loop() {
  static char my_message[ESP_NOW_MAX_DATA_LEN];     // received message
  static uint8_t sender_mac_addr[ESP_NOW_ETH_ALEN]; // sender MAC address
  static uint32_t my_message_num = 0;               // increments for each msg received unless UNI_REMOTE_RCVR_ERR_CBUF_MSG_DROPPED
  static uint16_t count_eyes = 0;
  uint16_t rcvd_len = 0; // the length of the message/command. If zero, no message.

  // get any message received. If 0 == rcvd_len, no message.
  esp_err_t msg_status = uni_remote_rcvr_get_msg(&rcvd_len, &my_message[0], &sender_mac_addr[0], &my_message_num);

#ifdef HANDLE_CERTAIN_UNLIKELY_ERRORS
  // we can get an error even if no message
  if (msg_status != UNI_REMOTE_RCVR_OK) { // (== ESP_OK)
    // handle error status here

    // these error codes come from set/clear flags; clear so can detect next time
    if ((UNI_REMOTE_RCVR_ERR_CBUF_MSG_DROPPED == msg_status) || (UNI_REMOTE_RCVR_ERR_MSG_TOO_BIG == msg_status)) {
      uni_remote_rcvr_clear_extended_status_flags();
    }
  }
#endif // HANDLE_CERTAIN_UNLIKELY_ERRORS

  // we can get a message with or without an error; see above uni_remote_rcvr_clear_extended_status_flags()
  // If 0 == rcvd_len, no message.
  if (rcvd_len > 0) {
    // process command
    do_esp_now_command(rcvd_len, my_message);
  }
  EVERY_N_MILLISECONDS( 5 ) { 
    led_pins_pwm(); // if needed, output brightness of LED
  } // end EVERY_N_MILLISECONDS 5

  EVERY_N_MILLISECONDS( 50 ) { 
    if (DFcheckSoundDone()) {
      if (MUSIC_MODE_TYPE_OF_SONG == g_music_mode) {
        // loop through array of songs
        uint16_t tmp_soundnum = 0xFFFF;
        uint16_t tmp_idx = g_music_type_list_idx_playing_now + 1;
        if (tmp_idx >= g_music_type_list->num_in_list) tmp_idx = 0;
        g_music_type_list_idx_playing_now = tmp_idx;
        tmp_soundnum = g_music_type_list->list_array[g_music_type_list_idx_playing_now];
        g_music_song_to_soundnum_idx_playing_now = find_music_idx_from_soundnum(tmp_soundnum);
        DFstartSound(tmp_soundnum, g_current_volume_set);
      } else /* if (MUSIC_MODE_SINGLE_SONG == g_music_mode) */ {
        // restart sound
        g_music_song_to_soundnum_idx_playing_now = find_music_idx_from_soundnum(g_music_soundnum_single_song);
        DFstartSound(g_music_soundnum_single_song, g_current_volume_set);
      }
    }
  } // end EVERY_N_MILLISECONDS 50

#if MDO_USE_OTA // if using Over-The-Air software updates
  EVERY_N_MILLISECONDS( 50 ) { 
    // if using Over-The-Air software updates
    mdo_ota_web_loop();
  }
#endif // MDO_USE_OTA if using Over-The-Air software updates

} // end loop()

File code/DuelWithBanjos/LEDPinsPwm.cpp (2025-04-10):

/* Author: https://github.com/Mark-MDO47  March 20, 2025
 *  https://github.com/Mark-MDO47/DuelWithBanjos
 *
 */

/*
   Copyright 2025 Mark Olson

   Licensed under the Apache License, Version 2.0 (the "License");
   you may not use this file except in compliance with the License.
   You may obtain a copy of the License at

       http://www.apache.org/licenses/LICENSE-2.0

   Unless required by applicable law or agreed to in writing, software
   distributed under the License is distributed on an "AS IS" BASIS,
   WITHOUT WARRANTIES OR CONDITIONS OF ANY KIND, either express or implied.
   See the License for the specific language governing permissions and
   limitations under the License.
 */

/*
 * This code is being developed to provide PWM LED Eye control for the
 * "DuelWithBanjos" project.
 *
 * It is a work-in-progress and incomplete at this time.
 *
 */

#include "LEDPinsPwm.h"

static uint16_t g_led_pin_pwm_dbg_step = 0;      // non-zero to do debug prints
static uint32_t g_led_pin_pwm_num_pwm_scale = 1; // zero turns off LEDs. numerator for pwm scaling
static uint32_t g_led_pin_pwm_den_pwm_scale = 1; // should never be zero! denominator for pwm scaling

/////////////////////////////////////////////////////////////////////////////////////////////////////////
// led_pin_pwm_set_dbg_enable() - routine for debugging
//
//   p_enable - nonzero to enable led_pin_pwm debug prints; zero to disable
//
void led_pin_pwm_set_dbg_enable(uint16_t p_enable) {
  g_led_pin_pwm_dbg_step = p_enable;
} // end led_pin_pwm_set_dbg_enable()

/////////////////////////////////////////////////////////////////////////////////////////////////////////
// led_pin_pwm_int_dbg_step() - internal routine for debugging, display steps at important steps
//
// void led_pin_pwm_int_dbg_step(int p_pin_idx); // to keep the compiler happy
void led_pin_pwm_int_dbg_step(int p_pin_idx) {
  static int first_time = 1;

  if (g_led_pin_pwm_dbg_step) {
    pwm_pin_info * my_pin_info = &g_pwm_pin_info[p_pin_idx];
    pwm_led_ptrn_step * my_step_ptr = &my_pin_info->ptrn_step_ptr[my_pin_info->idx_curr_step];

    if (first_time) {
      Serial.printf("led_pin_pwm_int_dbg_step:my_pin_info\tpin_num\tidx_curr_step\tcurr_pwm_val\tprev_pwm_val\tscale_factor");
      Serial.printf("\tscaledtm_tick_incr\tscaledtm_next_tick\tscaledtm_next_step");
      Serial.printf("\tled_pin_pwm_dbg_step:my_step_ptr\tidx_curr_step");
      Serial.printf("\tstart_set_pwm\tstep_incr\tstep_time\ttick_time\ttick_pwm\n");
    }

    Serial.printf("\t%d\t%d\t%d\t%d\t%ld", my_pin_info->pin_num, my_pin_info->idx_curr_step, my_pin_info->curr_pwm_val, my_pin_info->prev_pwm_val, my_pin_info->scale_factor);
    Serial.printf("\t%ld\t%ld\t%ld", my_pin_info->scaledtm_tick_incr, my_pin_info->scaledtm_next_tick, my_pin_info->scaledtm_next_step);
    Serial.printf("\txxx\t%d", my_pin_info->idx_curr_step);
    Serial.printf("\t%d\t%d\t%d\t%d\t%d\n", my_step_ptr->start_set_pwm, my_step_ptr->step_incr, my_step_ptr->step_time, my_step_ptr->tick_time, my_step_ptr->tick_pwm);

    first_time = 0; // so we can turn this on and off
  } // end if g_led_pin_pwm_dbg_step
} // end led_pin_pwm_int_dbg_step()

/////////////////////////////////////////////////////////////////////////////////////////////////////////
// led_pin_pwm_int_ledcWrite() - internal routine to write scaled pwm values 
//
// parameters:
//    p_pin_num   - which pin to output to
//    p_pwm_val   - pwm value to output
//
void led_pin_pwm_int_ledcWrite(uint16_t p_pin_num, uint16_t p_pwm_val); // to keep the compiler happy
void led_pin_pwm_int_ledcWrite(uint16_t p_pin_num, uint16_t p_pwm_val) {
  // force the order of operations so we don't overflow numerator calculation
  uint16_t pwm_scaled = (((uint32_t)p_pwm_val) * g_led_pin_pwm_num_pwm_scale) / g_led_pin_pwm_den_pwm_scale;
  // Serial.printf("DEBUG my ledcwrite pin=%d pwm=%d scaled=%d\n", p_pin_num, p_pwm_val, pwm_scaled);
  ledcWrite(p_pin_num, pwm_scaled);
} // end led_pin_pwm_int_ledcWrite()

/////////////////////////////////////////////////////////////////////////////////////////////////////////
// led_pin_pwm_int_set_pwm_num_den() - internal routine to set valid values for pwm scaling 
//
// parameters:
//   p_num_pwm_scale     - numerator for final pwm scaling
//   p_den_pwm_scale     - denominator for final pwm scaling - should NOT be zero
//
void led_pin_pwm_int_set_pwm_num_den(uint16_t p_num_pwm_scale, uint16_t p_den_pwm_scale); // to keep the compiler happy
void led_pin_pwm_int_set_pwm_num_den(uint16_t p_num_pwm_scale, uint16_t p_den_pwm_scale) {
  if (0 == p_den_pwm_scale) {
    Serial.printf("warning - init denominator for pwm scale specified as zero; both num and den changed to 1");
    g_led_pin_pwm_num_pwm_scale = g_led_pin_pwm_den_pwm_scale = 1;
  } else {
    g_led_pin_pwm_num_pwm_scale = p_num_pwm_scale;
    g_led_pin_pwm_den_pwm_scale = p_den_pwm_scale;
  }
} // end led_pin_pwm_int_set_pwm_num_den()
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

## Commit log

2025-03-13 switch to ESP WROVER 32 HW Serial2 from software serial
2025-03-14 start of KiCad
    [Battery_Power.kicad_sch, DuelWithBanjos.kicad_pcb, DuelWithBanjos.kicad_sch]
2025-03-16 pin assignments and schematic first cut
    [Battery_Power.kicad_sch, DuelWithBanjos.kicad_sch]
2025-03-20 update schematic
    [Battery_Power.kicad_sch, DuelWithBanjos.kicad_sch]
2025-03-20 add initialization of LEDC PWM for Banjo Player LED eyes
2025-03-21 add LEDC_steps.ino to develop PWM code
2025-03-21 LEDC_steps.ino debug print initialiation
2025-03-22 LEDC_steps.ino re-arrange structs
2025-03-23 LEDC_steps.ino add comments and checks for do_pin_pwm_init_ptrn()
2025-03-23 LEDC_steps.ino first indications that anything is working
2025-03-24 LEDC_steps.ino better but still strange
2025-03-26 LEDC_steps.ino fix indexing issue
    [LEDC_steps.ino]
2025-03-26 LEDC_steps.ino improve debug output, start preparing to make into mini-library
2025-03-27 do_pins_pwm.cpp restore some global replace errors
    [do_pins_pwm.cpp]
2025-03-28 start renaming DoPinsPwm to LEDPinsPwm
2025-03-28 start adding denominator and numerator for final pwm scaling
2025-03-28 added global pwm scaling
2025-03-29 demonstrate changes in both global pwm scale and pattern
2025-03-30 LEDPinsPwm.h improve wording
2025-03-30 DuelWithBanjos.ino now has minimum LEDPinsPwm installed
2025-03-31 #include <esp32-hal-ledc.h> // did not seem to help
2025-04-04 more EYES:PATTERN - OPPOSITE doesn't work
    [DuelWithBanjos.ino]
2025-04-04 fix bug in LEDPinsPwm.cpp
    [LEDPinsPwm.cpp]
2025-04-09 re-order LEDPinsPwm.h
2025-04-09 add some comments to LEDPinsPwmTemplate.ino
2025-04-09 save last call to led_pin_pwm_set_pwm_scale
2025-04-10 some final touches on led_pin_pwm_set_pwm_scale
2025-04-10 add connectors for skeletons, move deck chairs around
    [Battery_Power.kicad_sch, DuelWithBanjos.kicad_sch]
2025-04-13 move pins farther apart
    [Battery_Power.kicad_sch, DuelWithBanjos.kicad_sch]
2025-05-02 fix typo in comment
    [DuelWithBanjos.ino]
2025-05-03 allow upper/lower case parameter for commands
2025-05-08 KiCad V9.0.1
    [Battery_Power.kicad_sch, DuelWithBanjos.kicad_sch]
2025-05-15 start setup for VisualMicro OTA debugging, problem with setting volume
    [DuelWithBanjos.ino, SoundNum.h]
2025-06-07 fix some bugs in VOL: commands
    [DuelWithBanjos.ino]
2025-06-08 V1.0 schematic power update
    [Battery_Power.kicad_sch, DuelWithBanjos.kicad_sch]
2025-06-29 add skip command to skip to next thing in music type
    [DuelWithBanjos.ino]
2025-10-05 tweak LEDPinsPwm.cpp error messages
    [LEDPinsPwm.cpp]
2025-10-05 LEDPinsPwmTemplate some tweaks to debugging printouts
